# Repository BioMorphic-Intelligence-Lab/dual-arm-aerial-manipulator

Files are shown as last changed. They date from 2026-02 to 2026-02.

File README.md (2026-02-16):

# Dual Arm Omnidirectional Aerial Manipulator mechanical design
This directory contains an export of the design files used to construct the Dual Arm Omnidirectional Aerial Manipulator. The design was made using Autodesk Fusion360, and the full exported archive can be found in `Fusion archive`. For 3D printed, STEP and STL exports are provided in case access to Fusion360 is not available. For lasercut/waterjetcut plate material (the body panels), the DXF is provided along with the STEP and STL.

ICRA paper: https://arxiv.org/pdf/2602.10703 \
Associated software repository: https://github.com/BioMorphic-Intelligence-Lab/manipulator_assisted_landing

If you plan to create this aerial manipulator, I recommend that you have some basic tools like soldering iron and consumables, screwdriver kit (I used hex socket bolts for everything), tweezers, flat-nose pliers etc. A Bambulab X1 Carbon was used and I printed all the parts in PLA.

## Part list
The design is divided into 6 mechanical sub-assemblies. Per sub-assembly a part list is provided.

### Rotor arm (4x/6x)
The standard edition uses 4 of this entire assembly, however the upper and lower body plates provide attachment points for another set, making this design into a hexarotor.
| **Part name** | **Assembly** | **Part no.** | **Acquisition** | **Information** |
|---|---|---|---|---|
| Rotor Arm Clamp Upper | Rotor Arm | RA-01a | 3D print | |
| Rotor Arm Clamp Lower | Rotor Arm | RA-01b | 3D print | |
| Rotor Arm Rod | Rotor Arm | RA-02 | Buy/cut | Outer diam 14 mm, inner diam 12 mm |
| Motor Bracket Upper | Rotor Arm | RA-03a | 3D print | |
| Motor Bracket Lower | Rotor Arm | RA-03b | 3D print | |
| Motor | Rotor Arm | RA-04 | Buy | E-MAX PRO 2814 830KV |
| Propeller CW | Rotor Arm | RA-05a | Buy | GEMFAN 9045-3 CW |
| Propeller CCW | Rotor Arm | RA-05b | Buy | GEMFAN 9045-3 CCW |
| | | | | |

### Body
This assembly functions a bit like a bus, the structural attachment for all the other parts.
| **Part name** | **Amount** | **Sub-assembly** | **Part no.** | **Acquisition** | **Information** |
|---|---|---|---|---|---|
| Main Body Plate Upper | 2 | Body | DB-01 | Buy/waterjet cutting | Find a supplier that allows cutting from DXF. Thickness 2 mm. |
| Main Body Plate Lower | 2 | Body | DB-02 | Buy/waterjet cutting | Find a supplier that allows cutting from DXF. Thickness 2 mm. |
| Standoffs | 8 | Body | DB-03 | Buy | Length of 35 mm, threaded with M3. |
| Upper Cable Bridge | 1 | Body | DB-05 | 3D print | Optional but handy. |
| Lower Cable Bridge | 2 | Body | DB-06 | 3D print | Optional but handy. |
| ESC Bracket | 1 | Body | DB-07 | 3D print | Advise to modify to fit your ESC. |
| Electronics Bracket | 1 | Body | DB-08 | 3D print | |
| Leg | 4 | Body | DB-09 | 3D print | |
| Lidar/OF Plateau | 1 | Body | DB-10 | 3D print | |
| Antenna Holder | 1 | Body | DB-12 | 3D print | |
| Battery | 2 | Body | DB-15 | Buy | Any 2 identical 6S batteries should work. |

### Pivot Joint
The pivot joint is the most complex part and is a bit fiddly to put together. I printed everything out of PLA (including the gears) and it worked fine.
| **Part name** | **Amount** | **Sub-assembly** | **Part no.** | **Acquisition** | **Information** |
|---|---|---|---|---|---|
| Sun Shaft | 1 | Pivot Joint | PJ-01 | Buy/lathe | Use a strong material, I used steel but aluminium should work too. |
| Sun Gear | 2 | Pivot Joint | PJ-02 | 3D print | |
| Sun Bearing | 2 | Pivot Joint | PJ-03 | Buy | Outer diam 42 mm, inner diam 20 mm, width 12 mm. |
| Inner Sun Spacer | 1 | Pivot Joint | PJ-04 | 3D print | |
| Outer Sun Spacer | 2 | Pivot Joint | PJ-05 | 3D print | |
| Planet Shaft | 2 | Pivot Joint | PJ-06 | Buy | Solid aluminium axle diam 8 mm. |
| Planet Gear | 4 | Pivot Joint | PJ-07 | 3D print | |
| Planet Bearing | 8 | Pivot Joint | PJ-08 | Buy | Outer diam 16 mm, inner diam 8 mm, width 5 mm. |
| Inner Planet Spacer | 2 | Pivot Joint | PJ-09 | 3D print | |
| Outer Planet Spacer | 4 | Pivot Joint | PJ-10 | 3D print | |
| Drive Planet Gear | 2 | Pivot Joint | PJ-11 | 3D print | |
| Pivot Servo | 2 | Pivot Joint | PJ-12 | Buy | Feetech ST3025 |
| Pivot Clamp Lower | 2 | Pivot Joint | PJ-16 | 3D print | |
| Pivot Clamp Upper | 2 | Pivot Joint | PJ-17 | 3D print | |

### Shoulder Link (2x)
| **Part name** | **Amount** | **Sub-assembly** | **Part no.** | **Acquisition** | **Information** |
|---|---|---|---|---|---|
| Ring Gear | 1 | Shoulder Link | SL-01 | 3D print | |
| Shoulder Servo | 1 | Shoulder Link | SL-02 | Buy | Feetech STS3250 |
| Ring Gear Flange | 1 | Shoulder Link | SL-03 | 3D print | Glue on the Ring Gear |

### Upper Arm Link (2x)
| **Part name** | **Amount** | **Sub-assembly** | **Part no.** | **Acquisition** | **Information** |
|---|---|---|---|---|---|
| Upper Arm Link | 2 | Upper Arm | UA-01 | Buy/cut | Best is to find a supplier that cuts to specified length. Outer diam 14 mm, inner diam 12 mm. |
| Elbow Servo | 1 | Upper Arm | UA-04 | Buy | Feetech STS3235 |
| Servo Pulley | 1 | Upper Arm | UA-05 | 3D print | |
| Elbow Hinge | 1 | Upper Arm | UA-07 | 3D print | |
| Elbow Joint Spacer | 1 | Upper Arm | UA-08 | 3D print | |
| Elbow Servo Bracket Left  | 2 | Upper Arm | UA-09a | 3D print | |
| Elbow Servo Bracket Right | 2 | Upper Arm | UA-09b | 3D print | |
| Shoulder Connector | 1 | Upper Arm | UA-10 | 3D print | |
| Timing Belt | 1 | Upper Arm | UA-11 | Buy | Used RS timing belt, modify Servo Pulley accordingly. |
| Elbow Axle | 1 | Upper Arm | UA-12 | Buy/cut | Aluminium axle (same as Planet Shaft). |
| Torsion Bracket | 2 | Upper Arm | UA-14 | 3D print | |

### Forearm Link
| **Part name** | **Amount** | **Sub-assembly** | **Part no.** | **Acquisition** | **Information** |
|---|---|---|---|---|---|
| Forearm Link | 1 | Forearm | FA-01 | Buy/cut | 14x12 carbon fibre tube |
| Elbow Pulley | 1 | Forearm | FA-02 | 3D print | |
| Forearm Connector | 1 | Forearm | FA-03 | 3D print | |
| Elbow Flange | 1 | Forearm | FA-04 | 3D print | |
| Elbow Spacer | 1 | Forearm | FA-05 | 3D print | |
| Tube End | 1 | Forearm | FA-08 | 3D print | |

### Electronics
| **Part name** | **Amount** | **Sub-assembly** | **Part no.** | **Acquisition** | **Information** |
|---|---|---|---|---|---|
| ESC 4-in-1 | 1 | Electronics | EL-01 | Buy | T-Motor F55A Pro III 4in1 |
| Flight Controller | 1 | Electronics | EL-02 | Buy | Holybro Pixhawk 6X |
| Power Converter | 1 | Electronics | EL-03 | Buy | Matek PM20S-2 |
| Flight Computer | 1 | Electronics | EL-04 | Buy | Orange Pi 5B, but you can use any SBC like a Raspberry Pi |
| Servo USB-TTL board | 1 | Electronics | EL-05 | Buy | Feetech FE-URT-1 USB to TTL board |
| Receiver | 1 | Electronics | EL-06 | Buy | FrSky X8R |
| Optical Flow | 1 | Electronics | EL-07 | Buy | Holybro PMW3901 |
| Laser Rangefinder | 1 | Electronics | EL-08 | Buy | ST VL53L1X Lidar Rangefinder |

## Contributing
If you want to contribute, or copied the design to make some adjustments of your own that you want to share, just open an issue describing your addition and we'll figure out a way to merge.

## Support
You can get in touch with me by putting your question as an issue in this repository, or e-mailing at m.b.j.brummelhuis-1@tudelft.nl

## License
MIT License

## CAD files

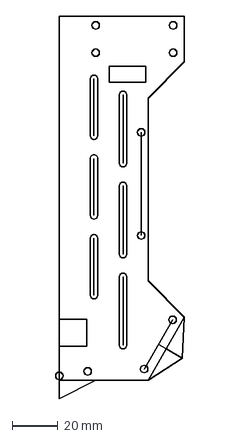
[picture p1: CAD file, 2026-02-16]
DXF/DB-01_UpperMainBodyPlate.dxf
56.6 x 168.0 mm

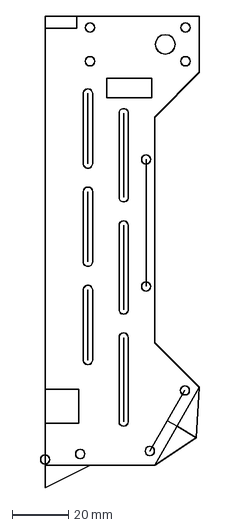
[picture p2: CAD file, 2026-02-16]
DXF/DB-02_LowerMainBodyPlate.dxf
56.6 x 168.0 mm

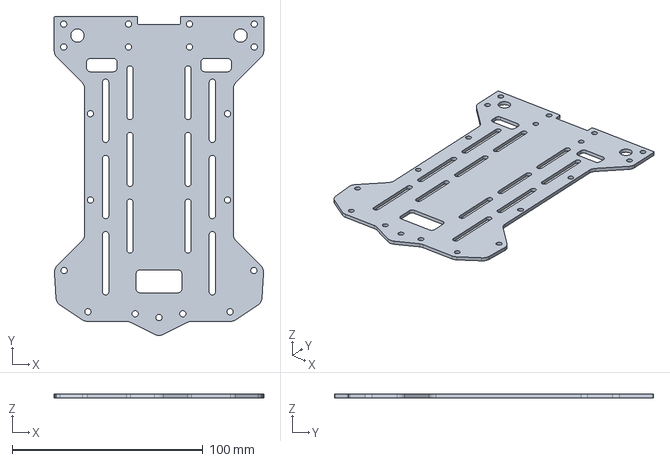
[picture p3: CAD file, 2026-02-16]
STEP/Body/DB-02_LowerMainBodyPlate.step
110.0 x 167.4 x 2.00 mm

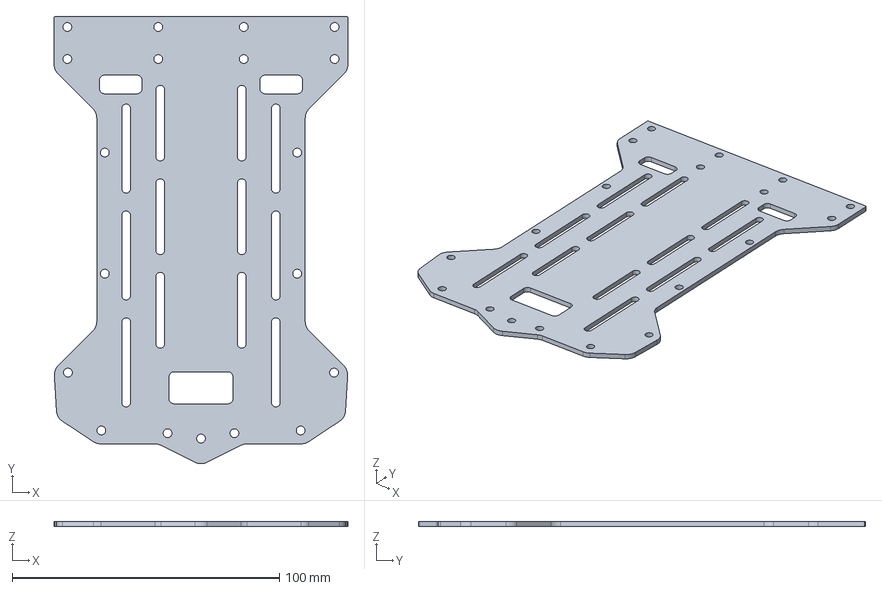
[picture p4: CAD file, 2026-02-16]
STEP/Body/DB-01_UpperMainBodyPlate.step
110.0 x 167.4 x 2.00 mm

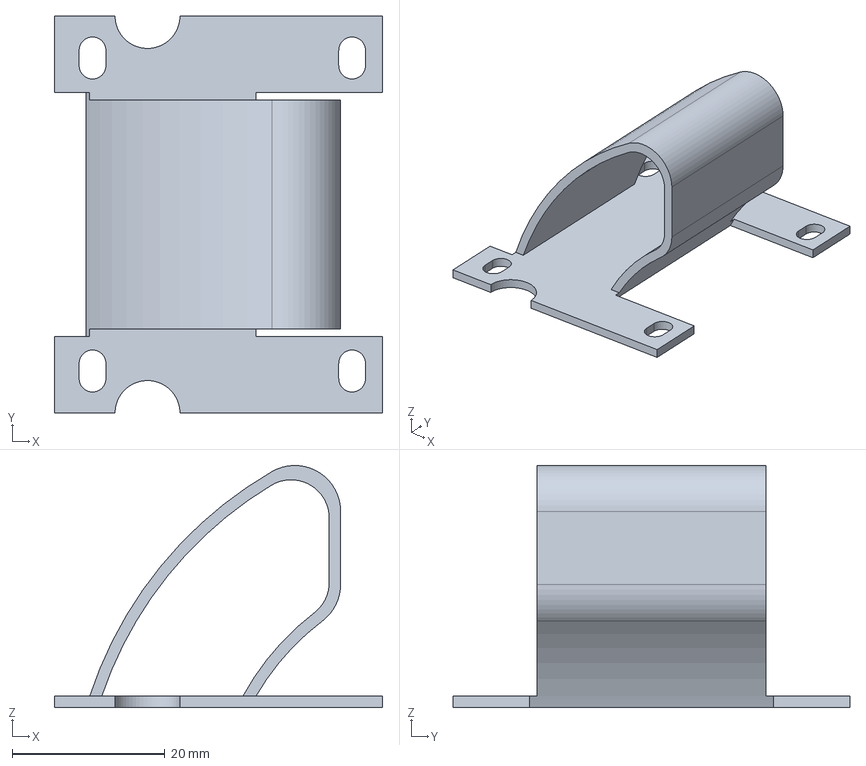
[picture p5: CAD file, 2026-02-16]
STEP/Body/DB-06_LowerCableBridge.step
43.0 x 52.0 x 31.7 mm

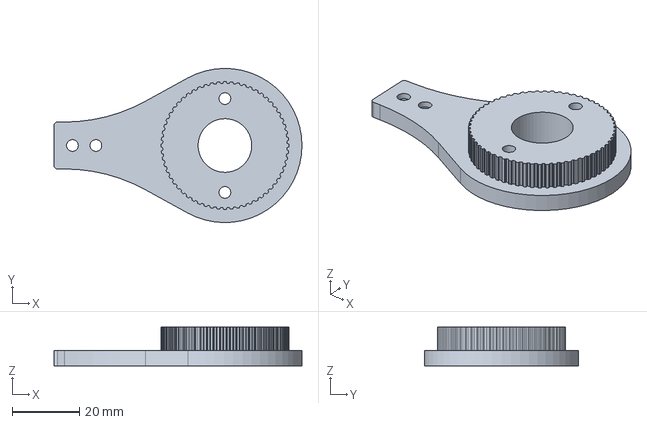
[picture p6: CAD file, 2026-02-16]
STEP/Forearm link/FA-02_ElbowPulley.step
74.0 x 46.0 x 11.5 mm

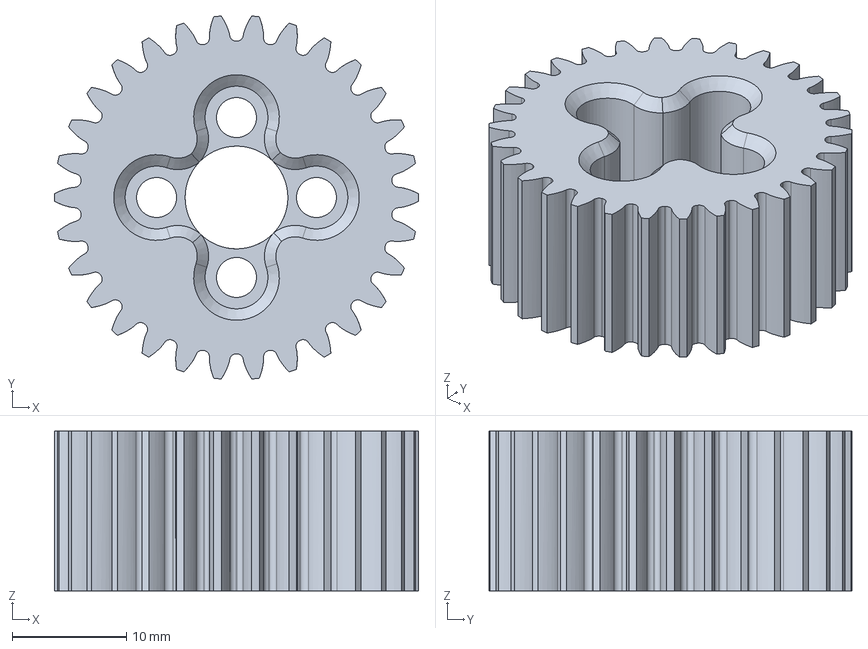
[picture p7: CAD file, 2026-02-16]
STEP/Pivot/PJ-11_DrivePlanetGear30.step
31.9 x 31.8 x 14.0 mm

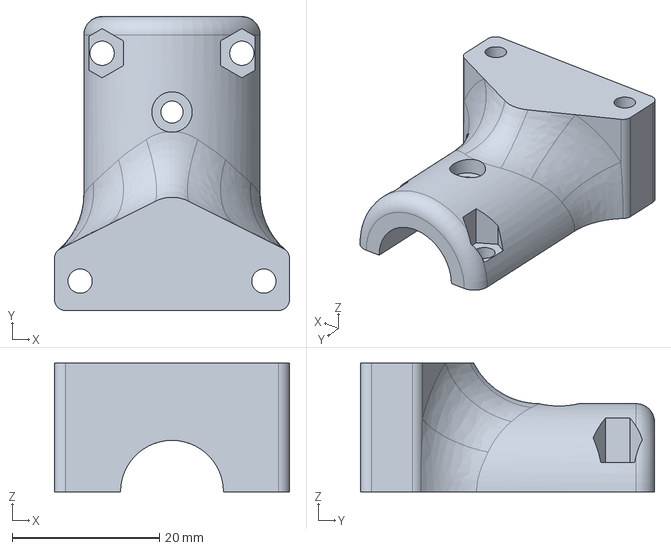
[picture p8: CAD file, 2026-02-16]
STEP/Rotor arm/RA-01b_RotorArmClampLower.step
32.0 x 40.0 x 17.5 mm

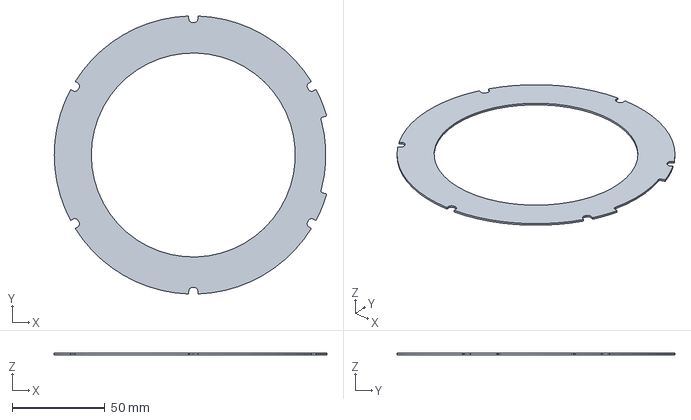
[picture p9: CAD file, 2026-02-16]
STEP/Shoulder link/SL-03_RingGearFlange.step
147.0 x 149.9 x 1.00 mm

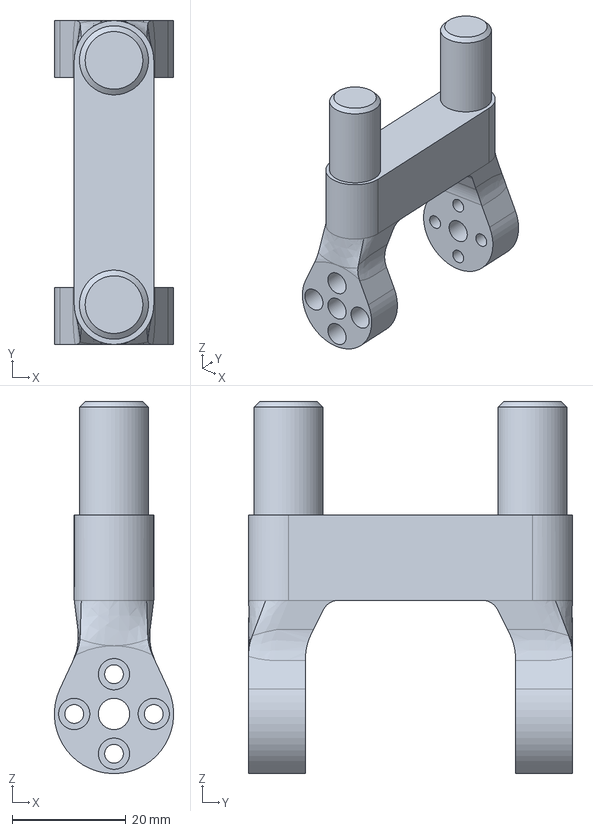
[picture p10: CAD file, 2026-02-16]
STEP/Upper arm link/UA-10b_SchoulderConnectorDouble.step
21.0 x 57.0 x 65.5 mm

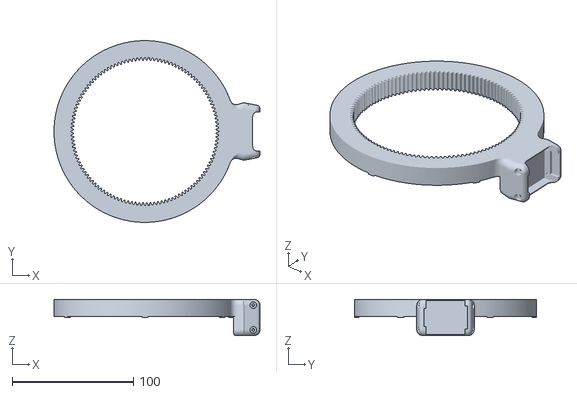
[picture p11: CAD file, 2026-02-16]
STL/Shoulder link/SL-01_RingGear120.stl
170.0 x 150.0 x 30.0

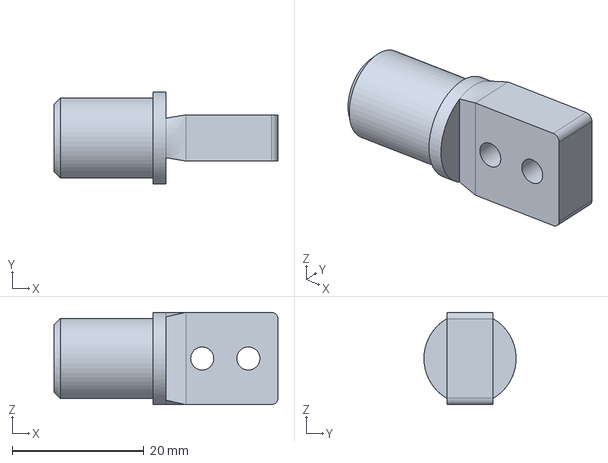
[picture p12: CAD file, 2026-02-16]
STEP/Forearm link/FA-03_ForearmConnector.step
34.0 x 14.0 x 14.0 mm

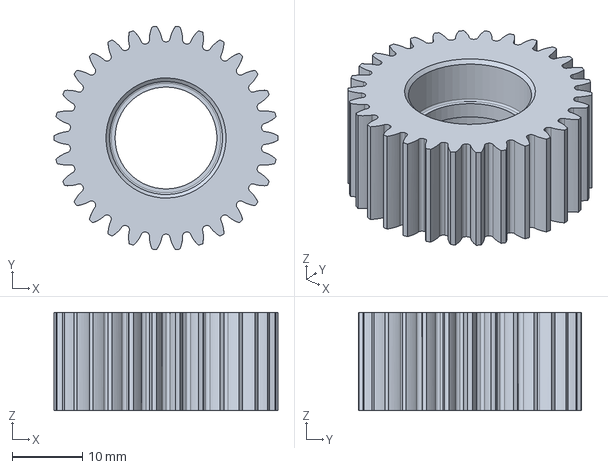
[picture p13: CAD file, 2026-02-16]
STEP/Pivot/PJ-07_PlanetGear30.step
31.9 x 31.8 x 14.0 mm

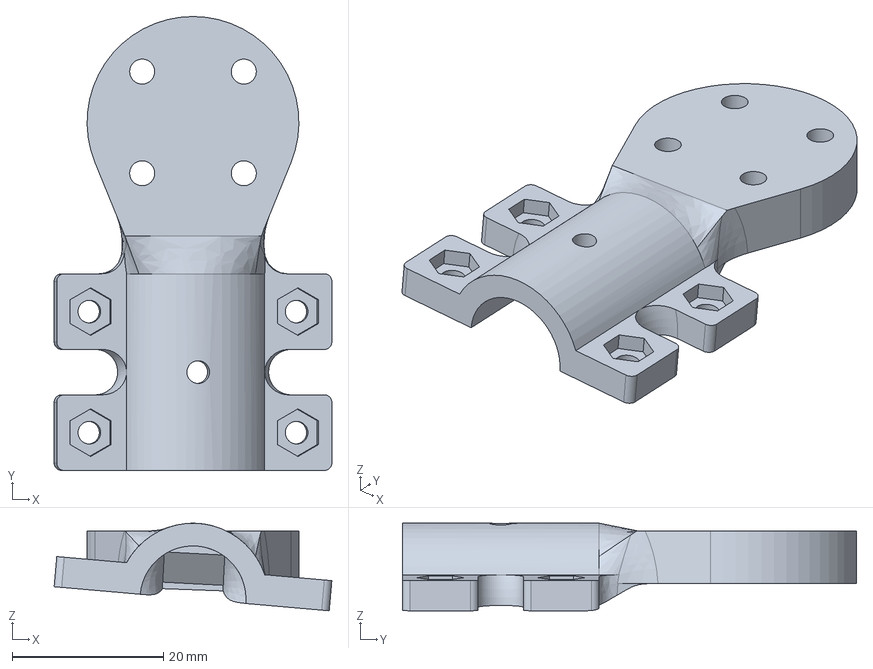
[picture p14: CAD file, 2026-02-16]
STEP/Rotor arm/RA-03b_MotorBracketLowerCCW5.step
36.7 x 60.0 x 11.6 mm

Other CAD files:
STEP/Upper arm link/UA-07_ElbowHinge.step
STEP/Body/DB-10_LidarOFPlateau.step
STEP/Forearm link/FA-04_ElbowFlange.step
STEP/Pivot/PJ-09_InnerPlanetSpacer.step
STEP/Body/DB-05_UpperCableBridge.step
STEP/Body/DB-07_ESCBracket.step
STEP/Body/DB-08_ElectronicsBracket.step
STEP/Body/DB-09_Leg.step
STEP/Body/DB-12_AntennaHolder.step
STEP/Forearm link/FA-05_ElbowSpacer.step
STEP/Forearm link/FA-08_TubeEnd.step
STEP/Pivot/PJ-02_SunGear60.step
STEP/Pivot/PJ-04_InnerSunSpacer.step
STEP/Pivot/PJ-05_OuterSunSpacer.step
STEP/Pivot/PJ-10_OuterPlanetSpacer.step
STEP/Pivot/PJ-16_PivotClampBottom.step
STEP/Pivot/PJ-17_PivotClampTop.step
STEP/Rotor arm/RA-01a_RotorArmClampUpper.step
STEP/Rotor arm/RA-03_MotorBracketUpper.step
STEP/Rotor arm/RA-03c_MotorBracketLowerCW5.step
STEP/Upper arm link/UA-05_ServoPulley.step
STEP/Upper arm link/UA-08_ElbowJointSpacer.step
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
